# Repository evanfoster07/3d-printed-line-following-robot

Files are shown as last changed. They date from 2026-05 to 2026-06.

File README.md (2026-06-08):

# 3D-Printed Line Following Robot

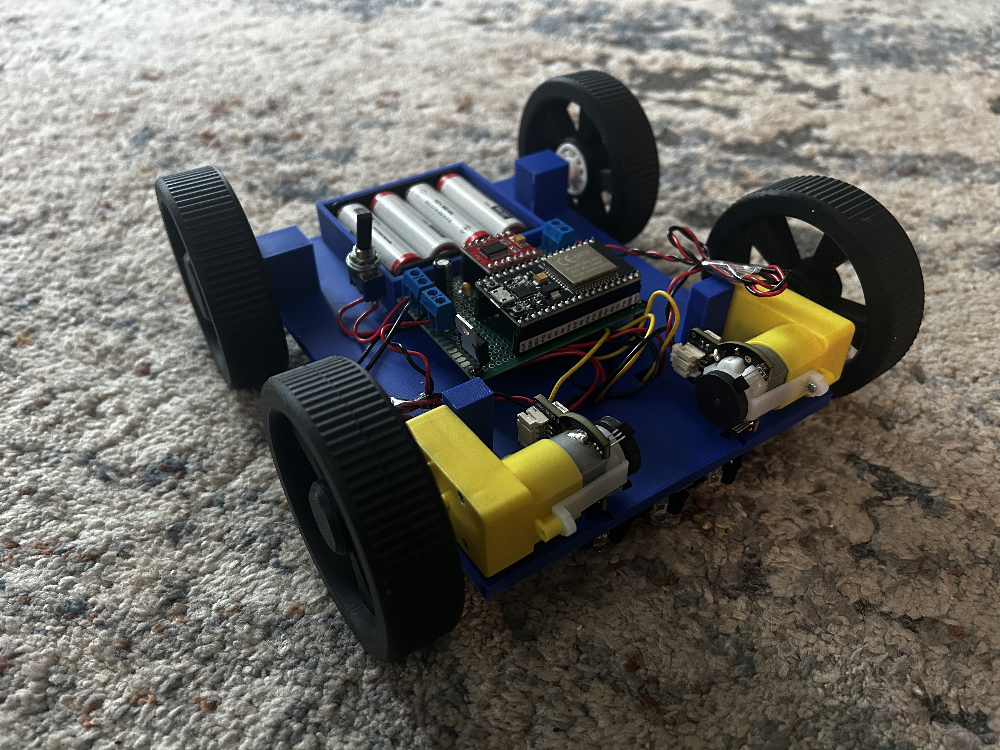
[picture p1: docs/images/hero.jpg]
Hero Image


This project is an autonomous line-following robot built around an ESP32, featuring a fully custom-designed and 3D-printed chassis.

The goal of this project was to design, build, and validate a complete embedded system from scratch, integrating mechanical design, electronics, and control logic into a working robotic platform.

## Project Video

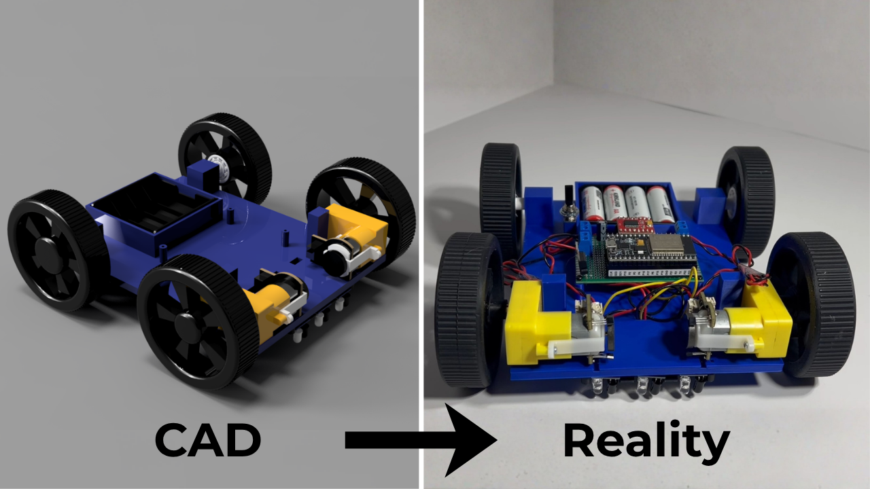
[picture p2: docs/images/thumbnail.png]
Watch the video (https://youtu.be/uBdEDjPaecE?si=iz57nBTeC71UOYvS)


Watch the full project video on YouTube

## Features 
- 3-sensor line detection system using IR reflectance sensors
- Differential drive control using TB6612FNG motor driver
- Custom 3D-printed chassis designed in Fusion 360
- Real-time line-following logic with recovery/search behavior
- Modular circuit design using perfboard and KiCad schematic planning
- Power stabilization using decoupling capacitors

## Hardware 
- ESP32 dev board
- TB6612FNG dual Motor driver 
- 2 DC motors
- 3 line sensors (IR reflectance sensors)
- 4 AA battery holder + batteries
- 5V regulator
- Capacitors (100µF electrolytic, 0.1µF ceramic)
- Power switch

## Mechanical Design

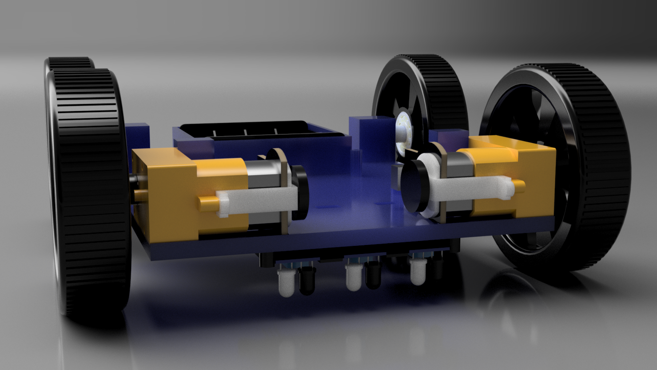
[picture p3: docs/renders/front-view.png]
Front View


- Fully custom chassis designed in Fusion 360
- Integrated mounts for:
    - Motors
    - Perfboard electronics
    - Battery holder
- Dedicated IR sensor mounting system:
    - Secure placement under chassis
    - Adjustable access to tuning potentiometers
- Wire routing channels built into chassis for cleaner assembly
- Tested multiple wheel and bearing configurations for stability

## CAD
The /cad directory includes:
- Fusion 360 source files (.f3d)
- Printable models (.3mf)

Custom-designed components:
- Chassis
- Sensor mount
- Front and rear wheels
- Hubcaps

Standard components (motors, sensors, battery holder) were modeled for fit and used in render but are not included.

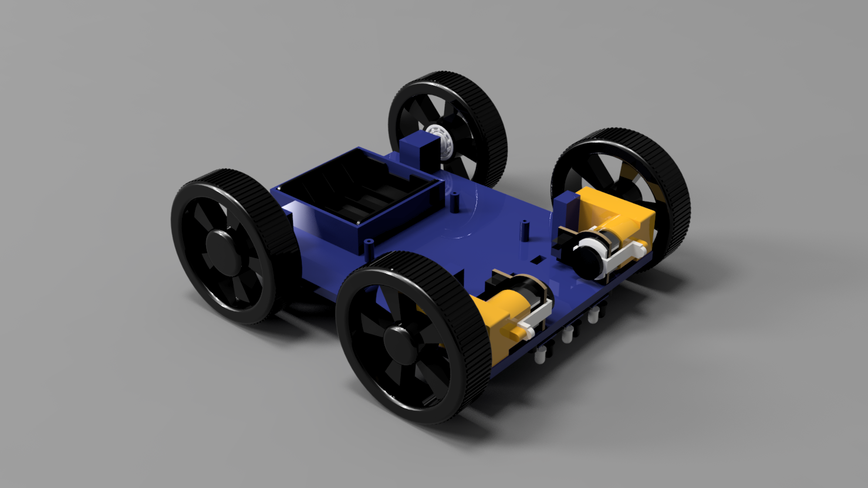
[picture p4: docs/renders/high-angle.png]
High Angle Render

*Overall CAD render of the robot chassis.*

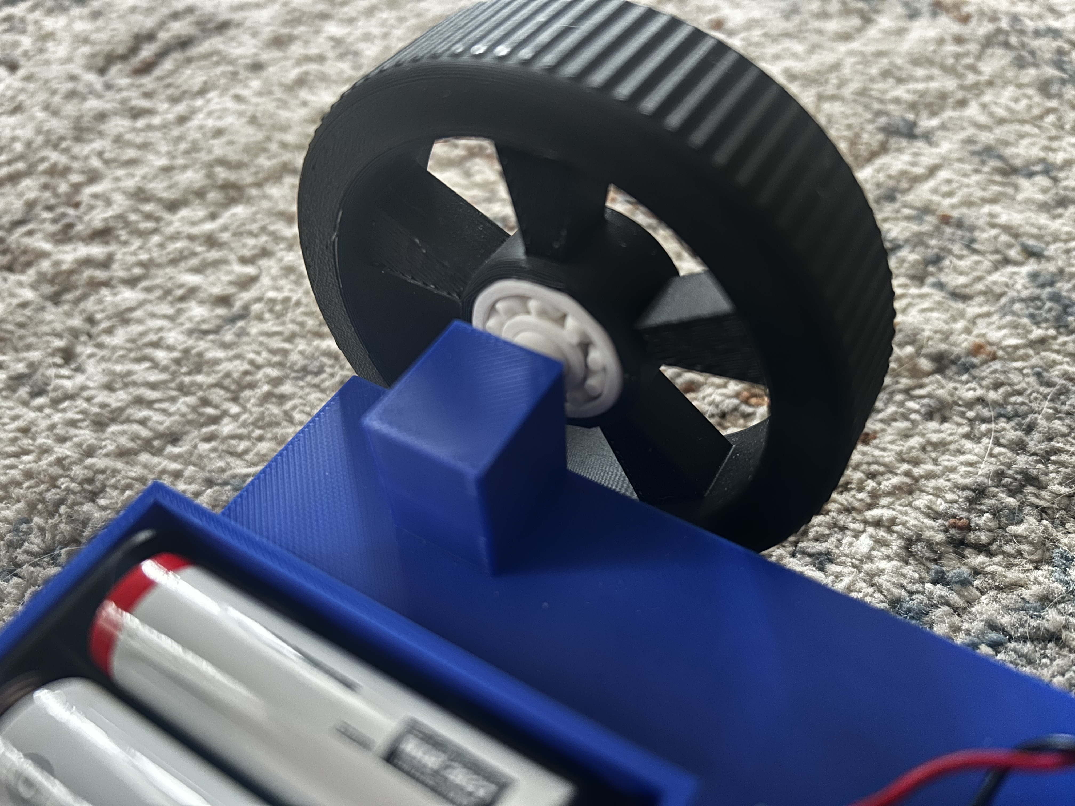
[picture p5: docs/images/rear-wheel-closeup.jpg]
Rear Wheel Closeup

*Close-up of rear wheel and bearing integration.*

## Electronics 

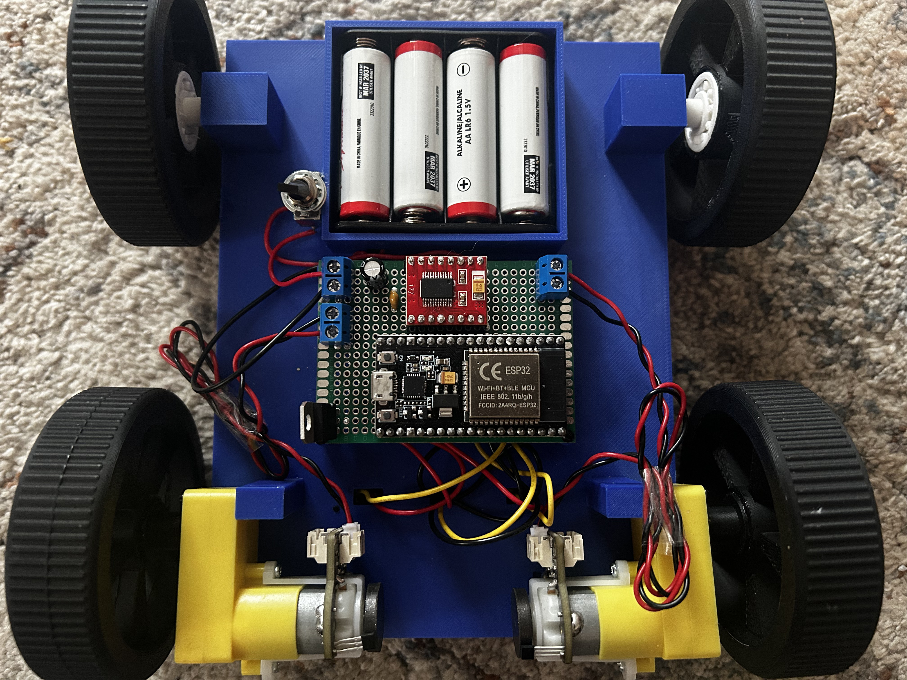
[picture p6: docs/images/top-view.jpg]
Electronics Overview


- Custom schematic designed in KiCad with simplified component models
- Use of net labels to improve schematic clarity and organization
- Perfboard implementation for final circuit assembly
- Key design considerations:
    - Shared ground between battery, ESP32, and motor driver
    - 5V regulation for logic components and ESP32
    - Decoupling (0.1µF) + bulk capacitance (100µF) for power stability

### Sensor Array
The robot uses a 3-sensor IR reflectance array mounted beneath the chassis for line detection. 
The custom mount provides stable positioning while maintaining access to sensor tuning potentiometers.

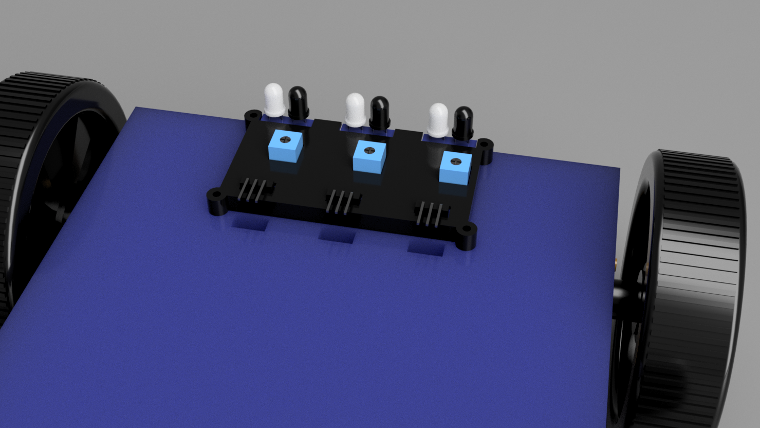
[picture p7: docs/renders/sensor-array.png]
Sensor Render


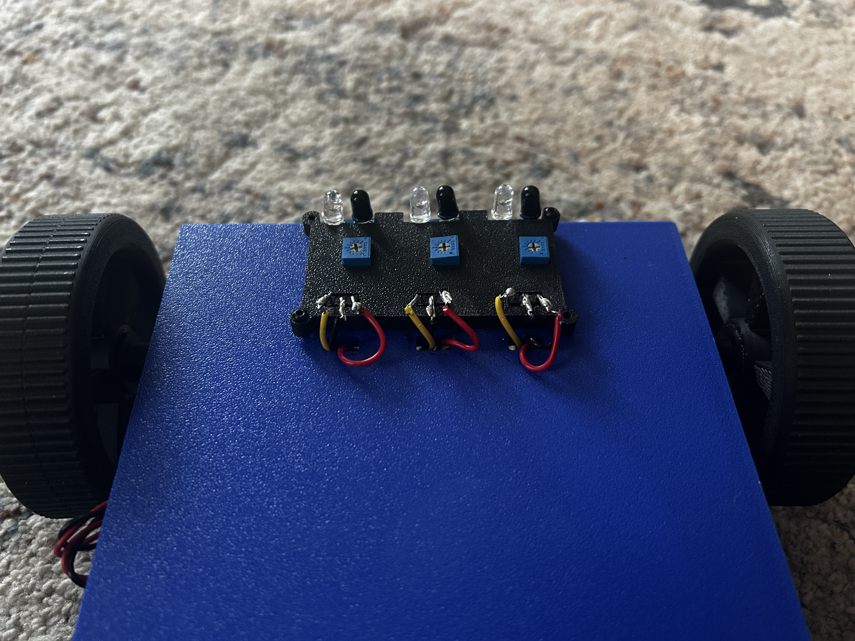
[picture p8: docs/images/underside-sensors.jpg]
Real Sensor Mount


### Schematic

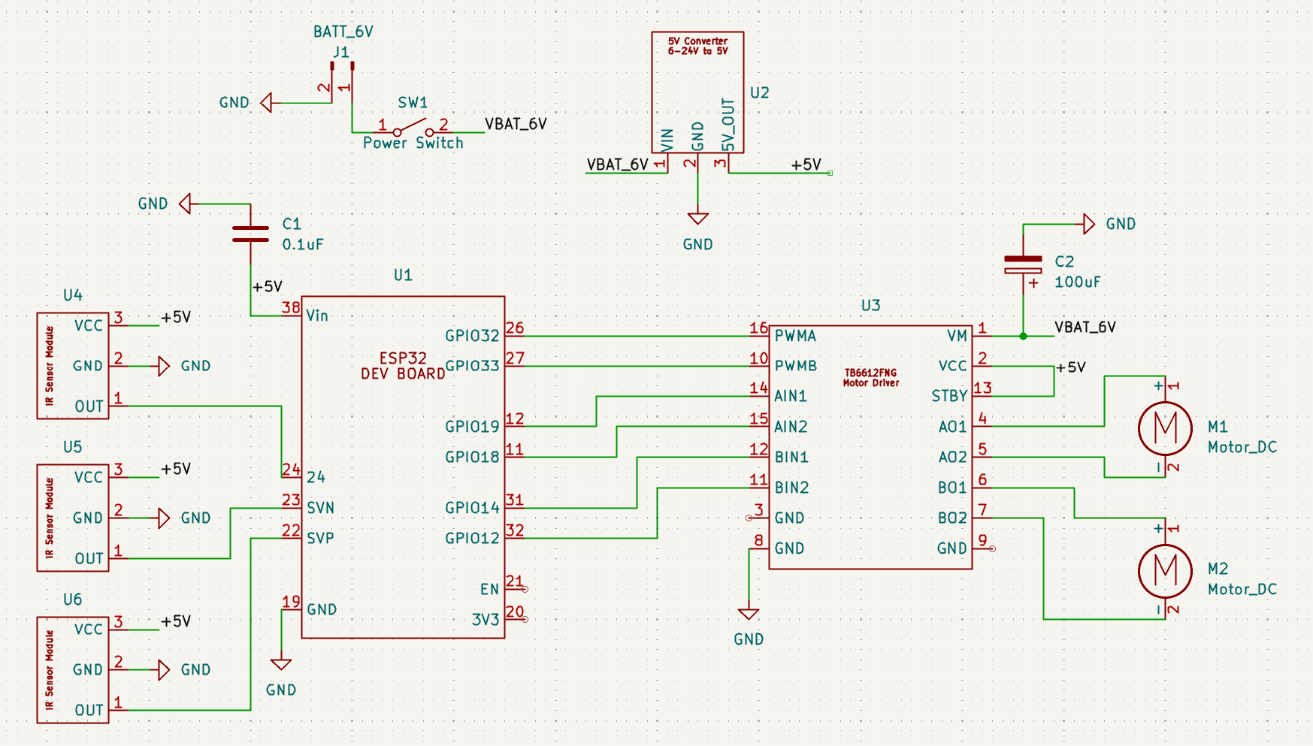
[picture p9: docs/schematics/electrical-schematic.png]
Electrical Schematic

*KiCad schematic used for circuit planning and perfboard implementation.*

## Control System
- Sensor readings processed in real time via ESP32
- Line-following logic based on prioritized sensor states
- Implemented fallback search behavior with a 1s timeout when line is lost

## Development Process
This project was developed iteratively, with hardware and software tested in stages:
- Prototyped and validated motors and driver independently
- Calibrated IR sensors using Serial Monitor feedback
- Designed and refined CAD components before full assembly
- Built and verified circuit incrementally on perfboard
- Integrated full system and performed real-world testing

## Challenges & Lessons Learned
- Power instability:
    - Experienced brownouts at startup due to voltage sag from motors
    - Highlighted importance of power distribution and decoupling
- Sensor calibration:
    - Required careful tuning to ensure consistent detection range
- Wiring complexity:
    - Reinforced importance of planning layout before soldering
- Schematic design:
    - Learned how net labels simplify complex circuits significantly
- CAD:
    - Iterated through multiple wheel and chassis designs to ensure proper fit and alignment
    - Designed mounting features to simplify assembly and reduce wire clutter

## Future Improvements 
- Implement PID control for smoother and faster line tracking
- Improve power delivery (separate motor supply or better regulation)
- Upgrade power supply from alkaline AA batteries to a higher-current rechargeable battery pack
- Design a custom PCB
- Add Bluetooth / remote control for selecting different behaviour modes
- Improve wire organization for maintainability and debugging 

## Credits 
- Rear wheel bearing model: https://www.printables.com/model/583731-print-in-place-ball-bearings

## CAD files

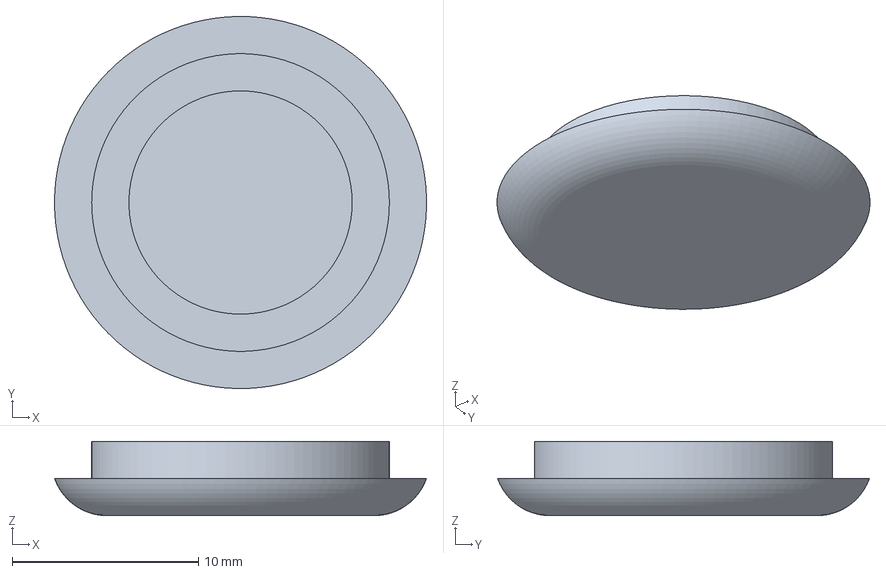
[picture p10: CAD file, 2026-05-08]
hardware/cad/exports/hubcap_front.3mf
20.0 x 20.0 x 4.00 mm

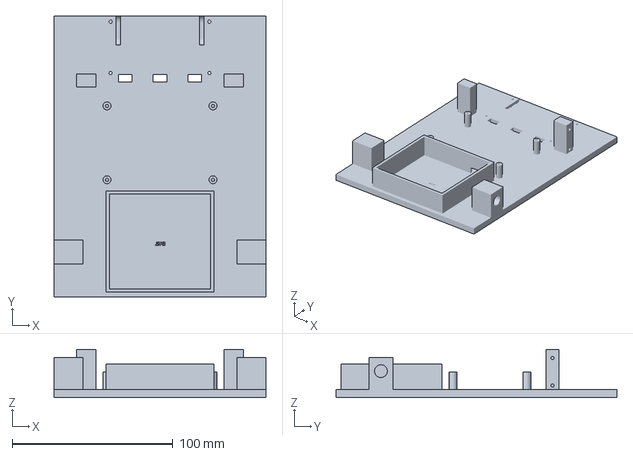
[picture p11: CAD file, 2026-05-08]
hardware/cad/exports/chassis.3mf
132.0 x 175.0 x 30.0 mm

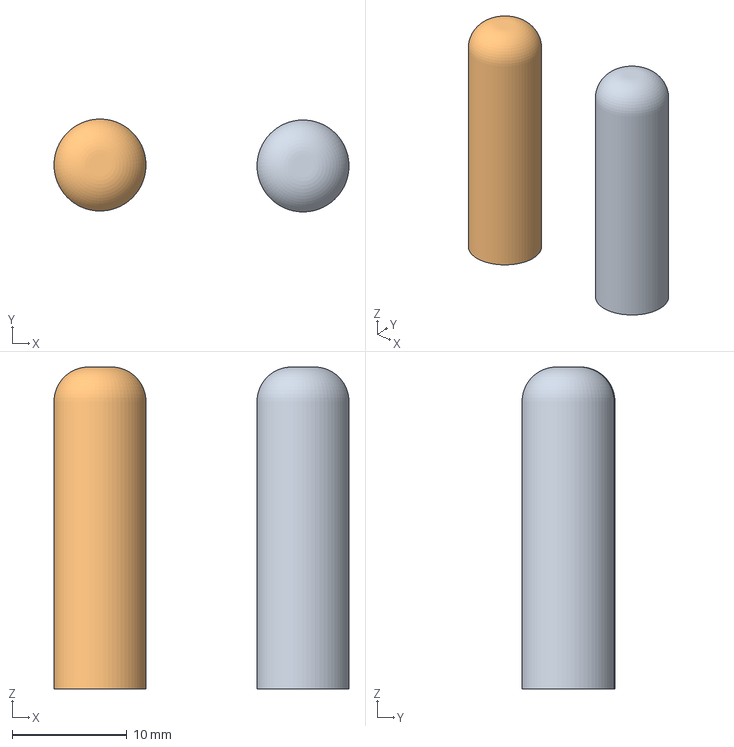
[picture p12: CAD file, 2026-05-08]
hardware/cad/exports/rear_wheel_shaft.3mf
25.6 x 8.08 x 28.0 mm

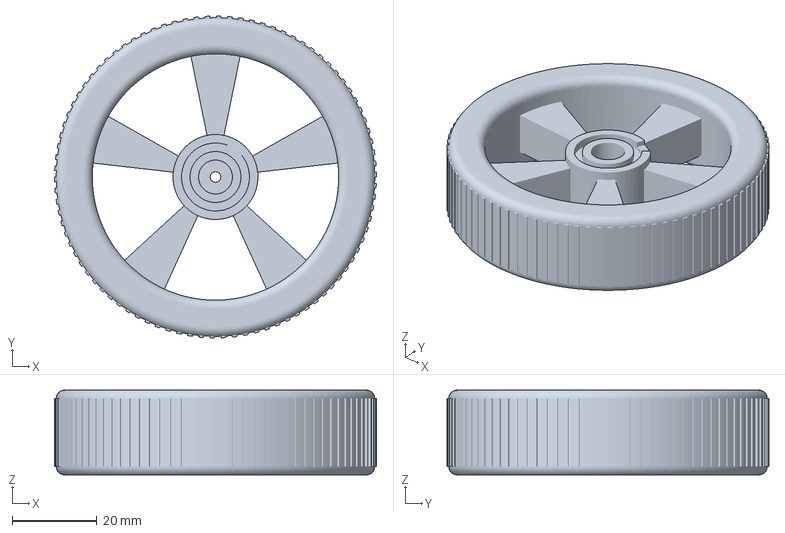
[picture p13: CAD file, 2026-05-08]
hardware/cad/exports/wheel_front.3mf
75.8 x 75.8 x 20.0 mm

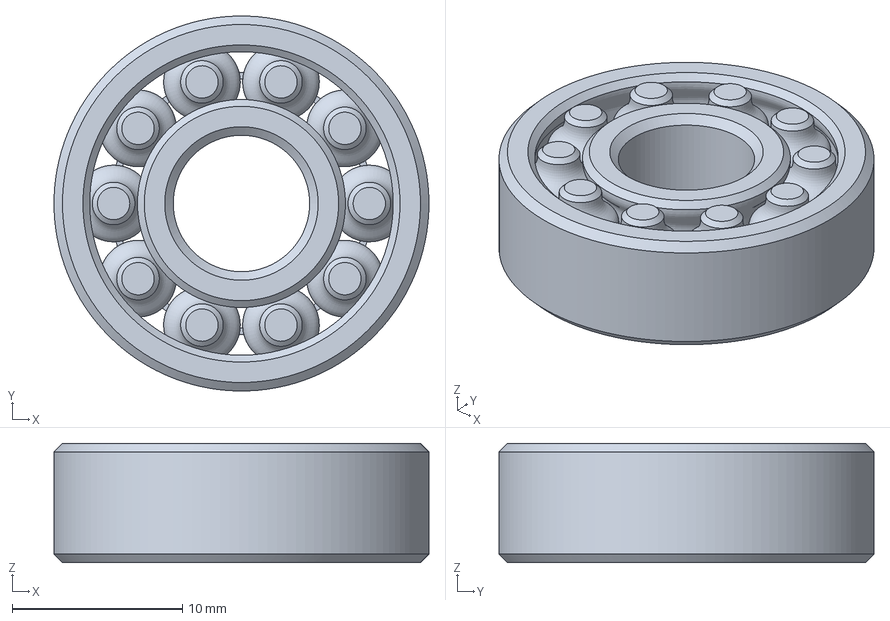
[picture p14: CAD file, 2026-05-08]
hardware/cad/exports/608_ball_bearing.3mf
22.0 x 22.0 x 7.00 mm

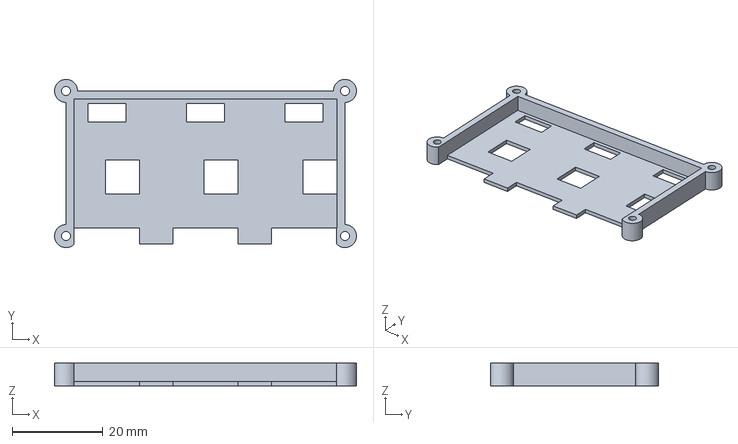
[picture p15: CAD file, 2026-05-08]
hardware/cad/exports/sensor_holder.3mf
66.6 x 37.1 x 5.00 mm

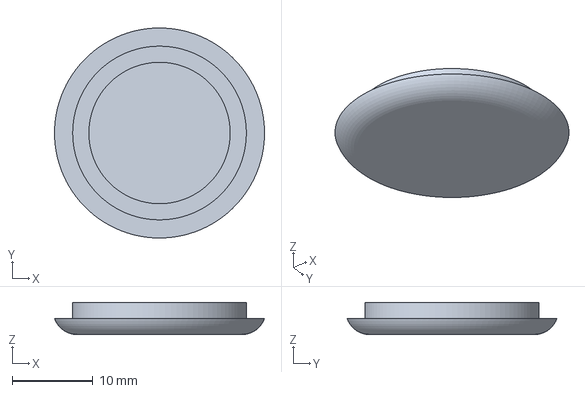
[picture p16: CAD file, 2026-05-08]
hardware/cad/exports/hubcap_rear.3mf
26.0 x 26.0 x 4.00 mm

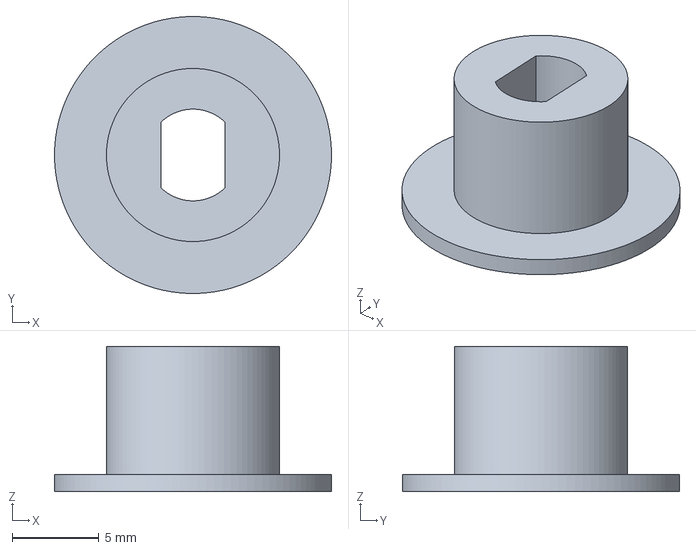
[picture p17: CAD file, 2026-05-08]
hardware/cad/exports/motor_shaft_slot.3mf
16.0 x 16.0 x 8.40 mm

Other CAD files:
hardware/cad/exports/wheel_rear.3mf
hardware/cad/source/chassis.f3d
hardware/cad/source/hubcap_front.f3d
hardware/cad/source/hubcap_rear.f3d
hardware/cad/source/motor_shaft_slot.f3d
hardware/cad/source/rear_wheel_shaft.f3d
hardware/cad/source/sensor_holder.f3d
hardware/cad/source/wheel_front.f3d
hardware/cad/source/wheel_rear.f3d

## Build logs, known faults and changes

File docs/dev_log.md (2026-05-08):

## Early April 
- Began CAD wheel modelling, testing prototypes, hubcap designs, and wheel shaft fits
- Tested online print-in-place ball bearing models for rear wheels 
- Designed chassis including the following features:
    - Motor and perfboard mounting spots using M2 screws
    - Battery holder with slots to accomodate wiring 
    - Slots in bottom of chassis to accomodate sensor wiring and screw holes for mounting
- Designed a IR sensor holder to mount onto bottom of chassis, allowing range potentiometer tuning while securing sensors
- Printed and assembled all mechanical components, ensuring proper alignment and fit

## April 15, 2026
- Soldered pins onto TB6612FNG motor driver modules and tested connections
- Verified motor driver function and tested motors with simple control test logic

## April 17, 2026
- Wired and tested sensors with breadboard and Serial Monitor readouts 
- Adjusted sensor potentiometers to equalize measurement distances 

## April 22, 2026
- Started circuit schematic and create custom simplified modules in KiCAD
- Next: Finish KiCAD schematic

## April 23, 2026
- Finished custom simplified KiCAD models and implemented in schematic
- Made wire connections in schematic and re-organized pin positions for readability
- Learned net labels greatly reduce wire clutter
- Next: finish soldering components onto perfboard and write control logic 

## April 29, 2026
- Finished soldering main motor driver / control logic 
- Attached switch to control battery power delivery
- Tested hardware on perfboard with simple code 
- Next: finish soldering (IR sensors) and implement line-following control 

## April 30, 2026
- Finished soldering IR sensor data and power wiring
- Tested sensor readings via Serial Monitor
- Implemented line-following control code
- Performed line-following tests with black construction paper 
- Implemented a search sequence when no sensors detect line 
- Issues: power brownouts began to occur at startup due to supply voltage sag despite power rail decoupling
- Next: finish documentation and confirm proper functionality with fresh batteries 

## May 2, 2026
- Completed the majority of GitHub README.md, including hardware, electronics, control system and design documentation 
as well as certain challenges and future improvements 
- Cleaned up control code and organized actively used / utility functions 
- Next: add CAD, hardware, and wiring images to GitHub repository and start demonstration video 

## May 4, 2026
- Duplicated CAD models and add colour for robot assembly render 
- Assembled coloured components in Fusion 360 
- Next: add previously mentioned images, record demo video and begin editing

## May 8, 2026
- Added real-life images and various robot CAD render perspectives to repo
- Recorded line-following action shots for demonstration video
- Next: begin video scripting and editing

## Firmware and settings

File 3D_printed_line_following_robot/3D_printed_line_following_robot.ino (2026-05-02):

const int sensor1 = 34; //P34
const int sensor2 = 39; //SVN
const int sensor3 = 36; //SVP 

const int LmotorPWM = 32; //P32
const int RmotorPWM = 33; //P33

const int LmotorDirA = 19; // P19
const int LmotorDirB = 18; // P18
const int RmotorDirA = 14; // P14
const int RmotorDirB = 12; // P12

void setup() {
  Serial.begin(115200);   // Debugging 

  pinMode(sensor1, INPUT);
  pinMode(sensor2, INPUT);
  pinMode(sensor3, INPUT);

  pinMode(LmotorDirA, OUTPUT);
  pinMode(LmotorDirB, OUTPUT);
  pinMode(RmotorDirA, OUTPUT);
  pinMode(RmotorDirB, OUTPUT);
  pinMode(LmotorPWM, OUTPUT);
  pinMode(RmotorPWM, OUTPUT);

  digitalWrite(LmotorDirA, LOW);
  digitalWrite(LmotorDirB, LOW);
  digitalWrite(RmotorDirA, LOW);
  digitalWrite(RmotorDirB, LOW);

  digitalWrite(LmotorPWM, LOW);
  digitalWrite(RmotorPWM, LOW);

  setSpeed(90);
}

int lastDirection = 0;
unsigned long searchStart = 0;
bool isSearching = false;

void loop() {
  //Line following logic 
  bool sensor1Stat = digitalRead(sensor1);
  bool sensor2Stat = digitalRead(sensor2);
  bool sensor3Stat = digitalRead(sensor3);

  if (sensor2Stat) {
    forwards();
    lastDirection = 0;
    isSearching = false;
  } else if (sensor1Stat) {
    turnLeft();
    lastDirection = -1;
    isSearching = false;
  } else if (sensor3Stat) {
    turnRight();
    lastDirection = 1;
    isSearching = false;
  } else {  //Search for line for 1s if no sensors are detecting 
    if (!isSearching) {
      searchStart = millis();
      isSearching = true;
      search();
    }
    
    if (millis() - searchStart < 1000) {
      search();
    } else {  //Stop searching after 1s 
      stop();
    }
  }
}


// =========================
//  Motor control functions 
// =========================

void forwards() {
  digitalWrite(LmotorDirA, LOW);
  digitalWrite(LmotorDirB, HIGH);
  digitalWrite(RmotorDirA, LOW);
  digitalWrite(RmotorDirB, HIGH);
}

void turnRight() {
  digitalWrite(LmotorDirA, LOW);
  digitalWrite(LmotorDirB, HIGH);
  digitalWrite(RmotorDirA, HIGH);
  digitalWrite(RmotorDirB, LOW);
}

void turnLeft() {
  digitalWrite(LmotorDirA, HIGH);
  digitalWrite(LmotorDirB, LOW);
  digitalWrite(RmotorDirA, LOW);
  digitalWrite(RmotorDirB, HIGH);
}

void setSpeed(int pwm) {
  analogWrite(LmotorPWM, pwm);
  analogWrite(RmotorPWM, pwm);
}

void stop() {
  digitalWrite(LmotorDirA, LOW);
  digitalWrite(LmotorDirB, LOW);
  digitalWrite(RmotorDirA, LOW);
  digitalWrite(RmotorDirB, LOW);
}

void search() {
  if (lastDirection == -1) {
    turnLeft();
  } else if (lastDirection == 1) {
    turnRight();
  } else {
    turnLeft(); //Default search
  }
}


// =================================
//  Utility/test functions (unused)
// =================================

void speedRampUp(int maxSpeed) {
  for(int speed = 0; speed < maxSpeed; speed++) {
    analogWrite(LmotorPWM, speed);
    analogWrite(RmotorPWM, speed);
    delay(1);
  }
}

void setSpeedLeft(int pwm) {
  analogWrite(LmotorPWM, pwm);
}
void setSpeedRight(int pwm) {
  analogWrite(RmotorPWM, pwm);
}

void backwards() {
  digitalWrite(LmotorDirA, HIGH);
  digitalWrite(LmotorDirB, LOW);
  digitalWrite(RmotorDirA, HIGH);
  digitalWrite(RmotorDirB, LOW);
}

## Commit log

2026-04-05 test IR sensor module with simple code
2026-04-11 Update README to reflect ESP32 instead of ESP8266
2026-04-17 motor speed/direction control test using TB6612FNG
2026-04-17 test sensor readings and add dev_log in docs file
2026-04-23 hardware: complete KiCAD schematic and update devlog
    [line_following_robot_schematic.kicad_sch]
2026-04-23 hardware: add bulk and decoupling capacitors to schematic
    [line_following_robot_schematic.kicad_sch]
2026-04-29 test: verify motor control on perfboard with simple test logic
    [line_following_robot_schematic.kicad_sch]
2026-05-08 Add .gitignore rules for KiCAD history and backups
2026-05-08 docs: add CAD files to repository and project images to README
    [608_ball_bearing.3mf, chassis.3mf, chassis.f3d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]
2026-05-08 docs: fix electrical schematic image file path in README
